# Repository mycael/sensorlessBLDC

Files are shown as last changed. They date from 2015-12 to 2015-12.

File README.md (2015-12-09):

# Sensorless Controller for BLDC Motor
Hardware and Software description for a sensorless BLDC Controller

**Please be careful**: _the controller is not yet fully tested and still requires development._

Hardware is designed with Altium Designer, source files are available in "Hardware" folder.
Software is written for dsPIC30F3011 in MPLABX IDE and is available in "Software" folder.
The Controller is currently tested on Turnigy D2836/8 1100kv motor.

___

## 1. General Characteristics
-	Current: 80A
-	Voltage: 10 to 20V (3S, 4S, and 5S Lipo) 
-	Power dissipation without heatsink : 300W
-	Speed setpoint set with PWM signal 
-	SPI 3 wires communication : an other board with MCU can access some informations (real motor speed, current consumption, etc ...)

___

## 2. Software Specifications

### Key points
* Firmware based on dsPIC30F3011
* Cycle frequency : 29 491 200 Hz (7.3728 MHz crystal with PLL 16x)
* Median filter to avoid command reading error

### Input PWM signal (speed setpoint) :

Crystal use instead of internal oscillator (as it's generally made on ESC) ensures a high precision reading of the speed setpoint coming from the PWM signal. 





In the equation above, *Speed* and *MaxMotorSpeed* are given in RPM (Revolutions per Minute), *PulseWidth* and *MaxPulseWidth* in µs (microseconde).

*Period* should be 25% greater than *MaxPulseWidth*

*MaxPulseWidth* and *MaxMotorSpeed* can be set in software in *general.h* file (see next part).

### Basic configuration
In the *general.f* file, you can change some parameters : 
- line 5 : You can adjust **motor** PWM frequency (min: 10kHz, max: 30kHz, default: 20Hz)
``` c 
#define   FPWM	  20000   // Hz
```

- line 8 : Set the maximum motor speed in RPM
``` c 
#define   MAX_MOTOR_SPEED     8000.0    // rpm
```

- line 11 : Set the speed at which the motor starts to spin (min: 2200, max: MAX_MOTOR_SPEED, default: 2200)
``` c 
#define   START_MOTOR_VALUE   2200	// rpm
```

- line 14 : Set the command pulse width which will correpond to the maximum motor speed (1)
``` c 
#define   MAX_PULSE_WIDTH     0.015   // sec 
```

(1) This controller can not perform clockwise or anticlockwise direction in the same application, under the start motor speed value (START_MOTOR_VALUE), the motor is stopped. To make the motor turns in an other direction, switch 2 phases between motor and controller.

### Advanced configuration
In the file *tuning.c*, you can change different parameter to enhance motor startup.

...
___

## 3. Hardware Specifications

### 3D view of the BLDC Controller: 

-	Top layer :

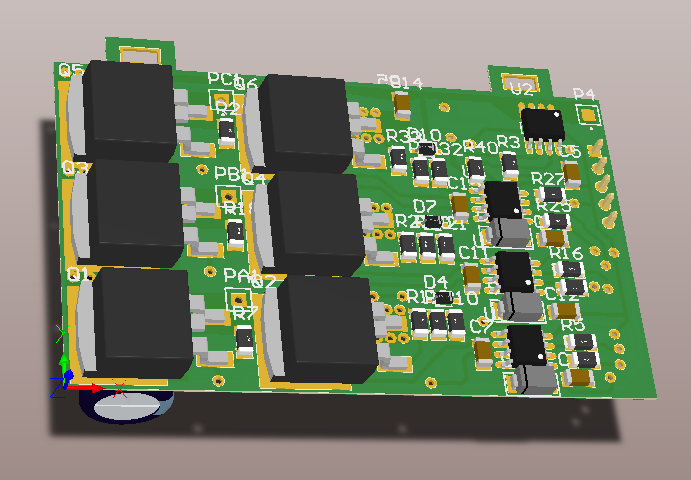
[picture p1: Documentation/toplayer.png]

-	Bottom layer :

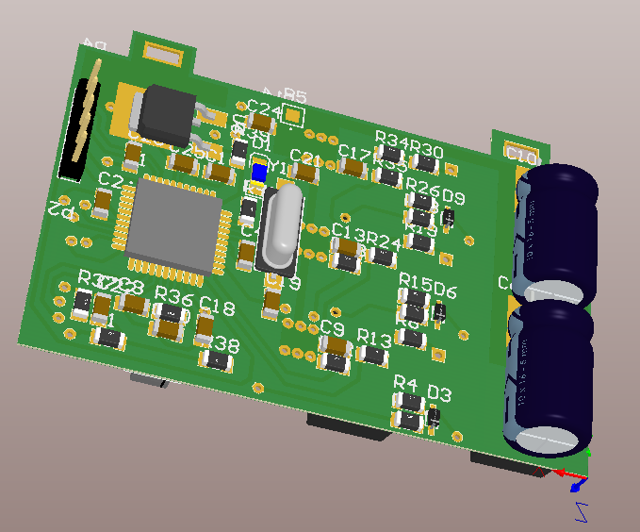
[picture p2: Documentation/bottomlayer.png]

- Dimensions : 

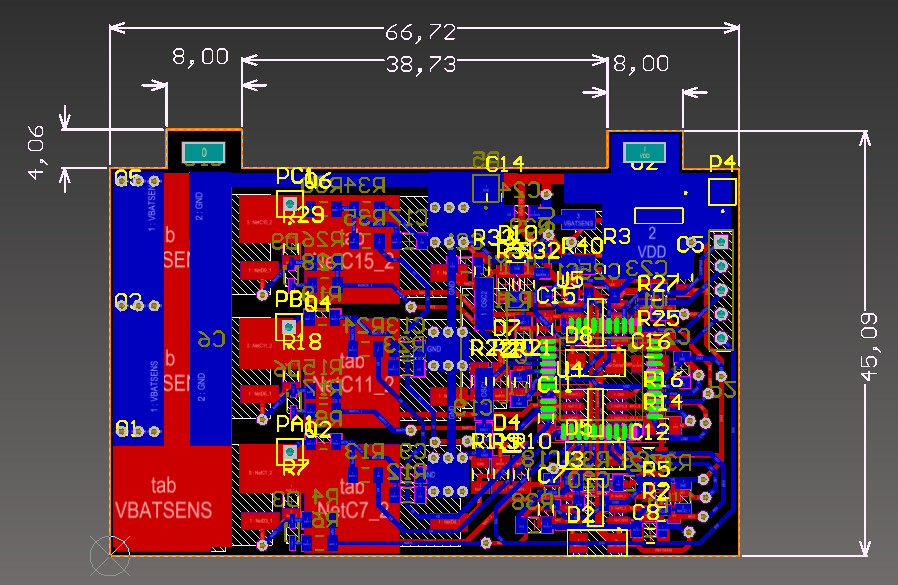
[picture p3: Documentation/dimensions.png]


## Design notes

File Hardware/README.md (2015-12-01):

# Sensorless BLDC Controller Hardware

Specifications :

CAO tool : 				Altium Designer

This folder contains the BLDC controller schematics and layout.

## MATERIAL LICENSE AGREEMENT:

<br /><span xmlns:dct="http://purl.org/dc/terms/" property="dct:title">Sensorless BLDC Controller schematics and layout</span> by <span xmlns:cc="http://creativecommons.org/ns#" property="cc:attributionName">Michael Guarisco</span> is licensed under a <a rel="license" href="http://creativecommons.org/licenses/by-nc/4.0/">Creative Commons Attribution-NonCommercial 4.0 International License</a>.

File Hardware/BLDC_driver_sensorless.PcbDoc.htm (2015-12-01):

Reporting Options

# File in Previous Format

Date | : | 18/11/2015
Time | : | 13:47:28
Filename | : | D:\GoogleDrive\workAltium\PCBs\BLDC_driver_sensorless\BLDC_driver_sensorless.PcbDoc

Version | Warning

This file was generated by an earlier version of the software

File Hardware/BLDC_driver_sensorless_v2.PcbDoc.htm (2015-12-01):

Reporting Options

# File in Newer Format

Date | : | 16/11/2015
Time | : | 16:14:44
Filename | : | D:\GoogleDrive\workAltium\PCBs\BLDC_driver_sensorless\BLDC_driver_sensorless_v2.PcbDoc

Version | Warning
Release 15.1 | CAUTION - Support Multi-line PCB Text added.
Release 16.0 | CAUTION - Pad/Via hole size tolerance value added.

This file was generated by a later version of the software

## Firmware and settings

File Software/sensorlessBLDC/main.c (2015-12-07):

/**********************************************************************
* Project Name :   sensorlessBLDC
* Processor:       dsPIC30F3011
* Compiler:        MPLAB XC16
*
* SOFTWARE LICENSE AGREEMENT:
* This software is based on a Microchip software. The Microchip Licence
* is applicable. As this software is distributed in a non commercial use
* it can bee freely modify or/and redistributed (see section :
* About Us » Legal Information » Copyright Usage Guidelines, on the
* Microchip website).
* 
* Microchip Technology Inc. (“Microchip”) licenses this software to you
* solely for use with Microchip dsPIC® digital signal controller
* products. The software is owned by Microchip and is protected under
* applicable copyright laws.  All rights reserved.
*
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
* REVISION HISTORY:
*~~~~~~~~~~~~~~~~~~~~~~~~~~~~~~~~~~~~~~~~~~~~~~~~~~~~~~~~~~~~~~~~~~~~~~
* Author            Date      Comments on this revision
*~~~~~~~~~~~~~~~~~~~~~~~~~~~~~~~~~~~~~~~~~~~~~~~~~~~~~~~~~~~~~~~~~~~~~~
* Reston Condit      Jan 7, 2007   Intial version
* Michael Guarisco   Nov, 2015     Modified version for dsPIC30F3011 and XC16
* Michael Guarisco   Dec 1, 2015       
**********************************************************************/

#include "general.h"
#include "hardware.h"
#include <libpic30.h>
#include "init_PWM.h"
#include "init_ADC.h"
#include "IIR_Filter.h"
#include "BEMF_filter.h"
#include "motor_isr.h"
#include "medium_event.h"
#include "dsp.h"
#include "init_IC.h"

// Setup Configuration bits
// FOSC
#pragma config FOSFPR = XT_PLL16        // Oscillator (XT w/PLL 16x)
#pragma config FCKSMEN = CSW_FSCM_OFF   // Clock Switching and Monitor (Sw Disabled, Mon Disabled)

// FWDT
#pragma config FWPSB = WDTPSB_16        // WDT Prescaler B (1:16)
#pragma config FWPSA = WDTPSA_512       // WDT Prescaler A (1:512)
#pragma config WDT = WDT_OFF            // Watchdog Timer (Disabled)

// FBORPOR
#pragma config FPWRT = PWRT_64          // POR Timer Value (64ms)
#pragma config BODENV = BORV20          // Brown Out Voltage (4.5V)
#pragma config BOREN = PBOR_ON          // PBOR Enable (Enabled)
#pragma config LPOL = PWMxL_ACT_HI      // Low-side PWM Output Polarity (Active High)
#pragma config HPOL = PWMxH_ACT_HI      // High-side PWM Output Polarity (Active High)
#pragma config PWMPIN = RST_IOPIN       // PWM Output Pin Reset (Control with PORT/TRIS regs)
#pragma config MCLRE = MCLR_DIS          // Master Clear Enable (Enabled)

// FGS
#pragma config GWRP = GWRP_OFF          // General Code Segment Write Protect (Disabled)
#pragma config GCP = CODE_PROT_OFF      // General Segment Code Protection (Disabled)

// FICD
#pragma config ICS = ICS_PGD            // Comm Channel Select (Use PGC/EMUC and PGD/EMUD)



int main ( void )
{
    int i, j;

    TRISD = 0x0001; // RD0 input for input capture
    TRISC = 0x0000;
  	LATC = 0;
  	LATD = 0;
  	TRISF = 0xFFFF;  
    RCON &= 0b0011111100100000;
    for(j=0; j<5; j++)
    {
        LED = 0;
        for(i = 0; i < 3; i++)__delay_ms(50);
        LED = 1;
        for(i = 0; i < 3; i++)__delay_ms(50);
    }
    LED = 0;
    
 	// Timer1 is used to measure
 	// the period between zero crossings.  Enable Timer 1.
 	T1CON = 0x8010;   // Setup Timer1 for 1:8 prescale.
    //T1CON = 0x8000;     // Setup Timer1 for 1:1 prescale.
 	
 	// Timer4 and Timer 5 will be the commutation timers.  They
	//  have the same prescaler (1:8) as Timer 1.  Turn on Timer 4
	//  but not Timer 5  
 	T4CON = 0x0010;			// 1:8 prescaler
    //T4CON = 0x0000;			// 1:1 prescaler
	TMR4 = 0;				// clear Timer 4
	IFS1bits.T4IF = 0;		// Disable the Timer 2 interrupt
	IEC1bits.T4IE = 0;
	T4CONbits.TON = 1; 		// Turn on Timer 2

	T5CON = 0x0010;			// 1:8 prescaler
    //T5CON = 0x0000;			// 1:1 prescaler
	TMR5 = 0;				// clear Timer 3
	IFS1bits.T5IF = 0;		// Disable the Timer 3 interrupt
	IEC1bits.T5IE = 0;


 	Init_PWM();				// initialize the PWM module
 	Init_ADC();				// initialize the ADC module
    Init_IC();
 	 	 	 	
	// Call the IIRTransposeFilterInit routine to zero out the state variables for each
	//  of the three phases
	IIRTransposeFilterInit( &BEMF_phaseA_Filter );
	IIRTransposeFilterInit( &BEMF_phaseB_Filter );
	IIRTransposeFilterInit( &BEMF_phaseC_Filter );

	// initialize the motor state variable to turn the motor off
	RunMode = MOTOR_OFF;
    
 	while(1)
 	{
		if(ControlFlags.MediumEventFlag)
			MediumEvent();				// execute start-up ramp or speed control loop
	}
}

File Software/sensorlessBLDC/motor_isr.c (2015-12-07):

#include "general.h"
#include "hardware.h"
#include "IIR_Filter.h"
#include "BEMF_filter.h"
#include "commutation_states.h"
#include "tuning.h"
#include "motor_isr.h"


// ----------------------Function prototypes ---------------------------
void CheckZeroCrossing(void);
unsigned int ThirtyDegreeTimeAverage(void);

// ----------------- Global Variable Declarations ----------------------
unsigned int pot;		    // stores the potentiometer value
unsigned int HalltoSector[8] = {-1,2,4,3,0,1,5,-1};
unsigned int SectortoState[6] = {STATE0,STATE1,STATE2,STATE3,STATE4,STATE5};
unsigned int HallState;		// Hall effect sensor state
int Sector = 0;				// Sector (0 - 5)
int OldSector;				// Stores old sector

int vpha, vphb, vphc, vbus;  // stores the ADC result for phase A, B, and C and the bus voltage measurement

unsigned int Timer1TimeoutCntr = 0;
unsigned int BlankingCount = 3;
unsigned int phase_advance = 0;
unsigned int SpeedPtr;
unsigned int RunMode = 0;
unsigned int SensorlessStartState = 0;
unsigned int MediumEventCounter = 0;
unsigned int SlowEventCounter = 0;
long accumulator_c;
int signal_average;
unsigned long Speed = 0;
int vpha_filtered_sample;
int vphb_filtered_sample;
int vphc_filtered_sample;
unsigned int NextSectorState;
unsigned int SixtyDegreeTime[6];
unsigned int OneEightyDegreeTime[16];

volatile struct ControlFlags ControlFlags;

unsigned int pos_ptr = 0;

unsigned int SpeedReference = 0;
unsigned int SpeedReferenceFil[3];
unsigned int fil_i=0;
unsigned int SpeedReferenceOld = 0;
unsigned int MotorOffCounter = 0;
unsigned int MotorOnCounter = 0;
unsigned long AccConsumption = 0;



/*---------------------------------------------------------------------
  Function Name: ADCInterrupt
  Description:   ADC Interrupt Handler
  Inputs:        None
  Returns:       None
-----------------------------------------------------------------------*/
void __attribute__((__interrupt__, no_auto_psv)) _ADCInterrupt( void )   // occurs at a rate of 81.920 kHz
{
	int i;
	/* reset ADC interrupt flag */
	IFS0bits.ADIF = 0; 


	if (BlankingCount)				// if the blanking count hasn't expired, feed the Back EMF
	{								// filters the last filtered Back EMF sample (rather than the unfiltered sample.)
		BlankingCount--;
		vpha = vpha_filtered_sample;
		vphb = vphb_filtered_sample;
		vphc = vphc_filtered_sample;

//		vpha = (3*vpha_filtered_sample + VPHABUF)>>2;  // This three lines can be used an a alternative to the 
//		vphb = (3*vphb_filtered_sample + VPHBBUF)>>2;  //  previous three lines
//		vphc = (3*vphc_filtered_sample + VPHCBUF)>>2;
	}
	else
	{
		vpha = VPHABUF;
		vphb = VPHBBUF;
		vphc = VPHCBUF;
	}

	// Get the bus voltage and do a little averaging
	vbus =  (vbus + VBUSBUF) >> 1;
    
    // Get current sensor value
    //AccConsumption += VCURRENTBUF;

	switch (RunMode)
	{
		case MOTOR_OFF:
			OVDCON = 0;
			break;
		case HALL_SENSOR_MODE:
			// Read the hall sensors.  This is only done If running sensored.
			// Read Hall sensors to get position.
			do
			{
				HallState = (PORTD >> 8) & 0x0007;
				Sector = HalltoSector[HallState];
				i++;
			} while((Sector == -1) && (i<4));
	
			if(Sector != OldSector)
			{
				Commutate(Sector);
				TMR4 = 0;
				IFS1bits.T4IF = 0;
			}
		case SENSORLESS_START:
		case SENSORLESS_RUNNING	:
			CheckZeroCrossing();
			break;
		default:
			if (RunMode > (NO_OF_RUN_MODES - 1))  RunMode = 0;
			break;
	}
}

/*---------------------------------------------------------------------
  Function Name: T1Interrupt
  Description:   T1 Interrupt Handler
  Inputs:        None
  Returns:       None
-----------------------------------------------------------------------*/
void __attribute__((__interrupt__, no_auto_psv)) _T1Interrupt( void ) 
{
	IFS0bits.T1IF = 0;
	if (Timer1TimeoutCntr++ >= NumOfTimer1TimeOuts)  // When Timer 1 overflows the algorithm is lost
	{
		IEC0bits.T1IE = 0;		// turn off Timer 1 and stop the motor
		RunMode = MOTOR_OFF;
	}
}

/*---------------------------------------------------------------------
  Function Name: T4Interrupt
  Description:   T4 Interrupt Handler
  Inputs:        None
  Returns:       None
-----------------------------------------------------------------------*/
void __attribute__((__interrupt__, no_auto_psv)) _T4Interrupt( void )  // TMR 2 is never turned on in Hall Mode
{
	TMR4 = 0;			   			// clear TMR4
	IFS1bits.T4IF = 0;

	if (RunMode == SENSORLESS_RUNNING)	
	{
		Sector++;						// Increment Sector (there are 6 total)
		if(Sector > 5) Sector = 0;
		Commutate(Sector);				// Change the PWM output for next sector
	}
}

/*---------------------------------------------------------------------
  Function Name: T5Interrupt
  Description:   T5 Interrupt Handler
  Inputs:        None
  Returns:       None
-----------------------------------------------------------------------*/
void __attribute__((__interrupt__, no_auto_psv)) _T5Interrupt( void )  // TMR 3 is never turned on in Hall Mode
{
	T5CONbits.TON = 0;     			// turn off TMR5
	TMR5 = 0;
	TMR4 = 0;		
	IFS1bits.T4IF = 0;	   		
	IFS1bits.T5IF = 0;
	IEC1bits.T5IE = 0;
	Timer1TimeoutCntr = 0;			// A commutation has occured so the Timer 1 timeout counter can be reset

	if (RunMode == SENSORLESS_RUNNING)	
	{
		Sector = NextSectorState;
		Commutate(Sector);				// Force commutation
	}
}

/*---------------------------------------------------------------------
  Function Name: PWMInterrupt
  Description:   PWM Interrupt Handler
  Inputs:        None
  Returns:       None
-----------------------------------------------------------------------*/

void __attribute__((__interrupt__, no_auto_psv)) _PWMInterrupt( void )  // Occurs every 50us or at a rate of 20kHz
{
	IFS2bits.PWMIF = 0;             // Clear the PWM interrupt flag
	
	if (++MediumEventCounter >= MEDIUM_EVENT_COUNTER_FIRE)  // Fire Medium event every 1ms
	{
		MediumEventCounter = 0;
		ControlFlags.MediumEventFlag = 1;
	}
	if (RunMode == SENSORLESS_START)
	{
		MediumEventCounter += 9;  // Fire Medium event every 100us in SENSORLESS_START mode
	}

}
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

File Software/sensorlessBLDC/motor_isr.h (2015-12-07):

// Function declarations
void Commutate(unsigned int sector);

// General definitions
#define NO_OF_RUN_MODES 5
	
// algorithm state definitions (Loaded in RunMode)
#define MOTOR_OFF 0
#define SENSORLESS_INIT 1
#define SENSORLESS_START 2
#define SENSORLESS_RUNNING 3
#define HALL_SENSOR_MODE 4

// sensorless start mode state definitions (loaded into SensorlessStartState)
#define LOCK1 0
#define LOCK2 1
#define RAMP_INIT 2
#define RAMP 3

// This bit structure provides mode flags
struct ControlFlags{
        unsigned	RunMotor:1; 	
        unsigned	HighSpeedMode:1;
		unsigned 	MediumEventFlag:1;
        unsigned   	:13;
}; 

extern volatile struct ControlFlags ControlFlags;
extern unsigned int ZeroCrossPeriodFalling[8];
extern unsigned int ZeroCrossPeriodRising[8];
extern unsigned int RunMode;
extern unsigned int SensorlessStartState;
extern unsigned int phase_advance;
extern int signal_average;
extern unsigned int pot;
extern int vbus;
extern int Sector;
extern unsigned long Speed;
extern unsigned int OneEightyDegreeTime[16];
extern unsigned int SpeedReference;
extern unsigned char comError;

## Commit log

2015-12-01 Initial issue
    [BLDC_driver_sensorless.PcbDoc, BLDC_driver_sensorless.PrjPcb, BLDC_driver_sensorless_logic.SchDoc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]
2015-12-02 Version 0.5
    Fcy : 29491200 Hz
    Optimized start up
2015-12-03 Median filter added on PWM input reference speed
2015-12-03 Median filter added on PWM input speed ref
2015-12-07 Version 6
    Commande moteur ok
    A faire version 7 : Ajouter mesure courant et transmission SPI
